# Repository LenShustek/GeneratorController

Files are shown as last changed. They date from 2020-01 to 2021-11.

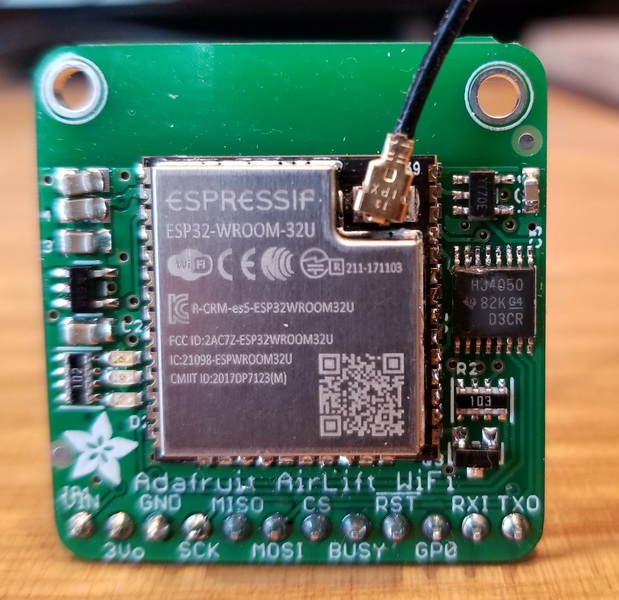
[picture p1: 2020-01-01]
photos/remade_Airlift.jpg

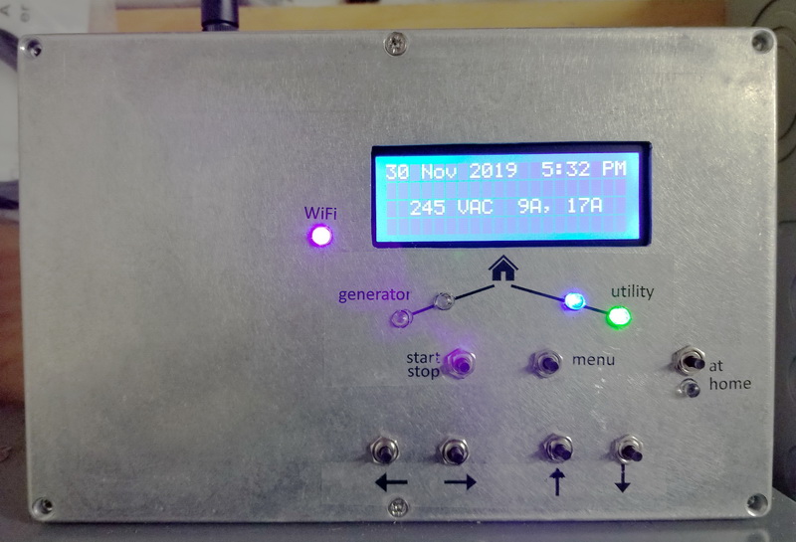
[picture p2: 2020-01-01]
photos/box_outside.jpg

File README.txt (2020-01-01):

This is the hardware and software design for an external custom 
controller for Cummins standby power generators and transfer switches. 

We have a couple of these generators in locations which are unoccupied 
for long periods of time. The normal operation of the standard 
setup is to run the generator whenever the power is out, until 
either the power returns or the fuel runs out. 

What we want instead, when the property is not occupied, is for the 
generator to run enough to keep the food in the freezers cold, but not 
to run all the time. That conserves fuel, and annoys the neighbors less. 

Our custom controller works like this: after the power fails, it waits 
for a few hours to see if the power comes back. If it doesn't, it runs 
the generator for 30 minutes every few hours so that the freezers are 
kept cold. If someone is home and wants the power to be on all the time, 
there is an "at home" button on the front panel that does that. All the 
times are, of course, configurable. 

The controller also has a WiFi interface and acts as a web server, so 
you can use a browser from a remote location to check the status and 
make changes. (That depends, of course, on whether your location has 
internet access without utility power or when on generator power.) It 
can also send a text message and/or an email when power fails or is 
restored, using the IFTTT ("If This Then That") free service. 

Other features:
  - display of the utility and generator voltage levels (0-250 VAC)
  - display of the load current on each of two phases (0-100A)
  - display of the starter battery voltage after the power fails,
    when it is not being charged
  - a configurable generator exercise schedule
  - a realtime clock with battery backup
  - non-volatile memory for configuration information and an event log
  - a hardware watchdog timer that restarts the processor if something 
    locks up the controller
  - manual operation of the generator and transfer switch for testing
  
We have this installed and running with these two generator/switch configurations:
  - Cummins RS22 22 kW generator with the RA100A automatic transfer switch
    (smart generator, dumb switch)
  - Cummins RS30000 30 kW generator with the RSS100 automatic transfer switch "with controller"
    (dumb generator, smart switch)
  
See more information in the "design notes" file and in the source code comments.

This is a non-trivial amateur construction project, and the design here comes, of course,
with no guarantee that it will work for you. That said, we are happy with the way it 
works for us.

Len Shustek
December 2019

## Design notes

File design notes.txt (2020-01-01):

DESIGN NOTES FOR A CUSTOM CUMMINS GENERATOR CONTROLLER

Which generators and transfer switches I'm using
------------------------------------------------

I built two of these controllers for two locations with different equipment from 
Cummins. In all cases, note that the ATS ("automatic transfer switch") design 
only allows it to switch to a supply (utility or generator) that has power. 

(1) RS22 22 kW generator and the RA100A transfer switch 

In this case the generator is smart; it controls an engine cooldown period and 
maintains its own exercise schedule. It responds to a "start generator" command 
and provides a "generator ready" status. 

The switch is dumb and only reacts to an "activate switch" input. It supplies 
contact closures to indicate which way the switch is positioned, and whether the 
utility power is present. We install only voltage and current sensors in the 
switch, plus a bunch of wires. 

(2) RS30000 30 kW generator and the RSS100 transfer switch "with controller" 

In this case the generator is primitive; it obeys a "start generator" command 
and does nothing else. No exercise periods, no engine cooldown, no "generator 
ready" status. 

The switch, on the other hand, is smart, with a microprocessor and some lights 
and buttons. Their processor chooses the switch position, starts the generator, 
enforces a cooldown period, and can establish an exercise schedule. We take over 
the "generator start" line, but otherwise let the switch processor do its 
thing. Our "connect to generator" relay output is not used. In addition to 
voltage and current sensors, we install relays that provide contact closures so 
we know whether utility and/or generator power is present. 

When power fails, the ATS waits for generator power to be present before 
activating the switch. Since we might delay starting the generator, it will 
follow that delay. When we "rest" the generator, it leaves the switch alone as 
long as utility power isn't present. The result is that our normal 
"wait-run-rest-run" cycle works fine. 

When utility power returns, it waits for TDEN ("time delay emergency to 
normal"), which defaults to 10 minutes, before switching back to utility power. 
Our "utility return delay" should therefore be at least that long so we don't 
turn off the generator prematurely. See the Cummins "RSS100 and RSS200 Transfer
Switch Service Manual" for instructions on setting TDEN to 5 minutes instead.

We have taken over the "generator start" control line, so we need to implement 
both an exercise schedule and an engine cooldown time, because their controller 
can no longer do those. 

In a future version of the controller we could add a third relay so that we can 
separately control "connect to utility" and "connect to generator"; then we are 
not dependent on the TDEN 10 minute delay to connect to the utility. That would
require that we connect those control lines to us instead of their processor.
It may not be worth it.

Changes we make inside the ATS (automatic transfer switch) include:
-------------------------------------------------------------------

 - connect our control/status and sense wire harnesses to various points
   inside the switch
 - add a toggle switch that powers down our controller and returns to 
   the normal factory mode of operation
 - add two ferrite transducers around the house power cables that 
   measure current draw of the load
 - add two transducers that measure the generator and utility voltage
 - for the RSS version, add two 240 VAC relays to indicate whether 
   utility and/or generator power is present
 
Design of the controller board
------------------------------

On one side of the PC board there are 7 pushbutton switches, a 20x4 LCD display, 
and 6 LED indicators. It mounts directly to the front panel of the metal 
enclosure using the switch nuts. The panel has holes for the switches and LEDs, 
and a rectangular cutout for the LCD display. 

The other side of the board contains all the other components including the two 
harness connectors to the transfer switch, and the Wifi antenna connection on 
the Airlift Wifi board. Many of the components are surface-mount, but I chose 
largish versions (1/4 watt resistors instead of 1/8 watt, for example) so that 
it's relatively easy to hand solder. 

The Airlift board is a special version of the Adafruit product I built which 
uses the ESP32 version that has a U.FL connector for an external antenna. 

Electrical noise mitigation
---------------------------

Being located adjacent to a box where 100+ amps of power is switched in 
milliseconds causes all sorts of wired and wireless RFI electrical noise 
that can disrupt the electronics of our controller. Here are the steps 
I took to mitigate that problem: 

- a metal enclosure for the circuit board
- an MOV transient voltage suppressor on the power input
- a large low-pass inductor and big filtering caps on the power input
- a diode array transient voltage suppressor on signals from outside the box
- optical isolation for digital input signals
- ground plane pours on both side of the PC board
- transparent conductive film over the cutout for the LCD display
- a deadman watchdog timer that resets the processor if it becomes catatonic
- code that resets the LCD display whenever the power is switched

That seems to have fixed the problem, but I have no idea which items were 
most important and how much margin there is.

Len Shustek
December 2019

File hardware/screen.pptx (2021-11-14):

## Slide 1

7.9”

power went off at
12 Mar 9:23 AM
generator goes on in
1 hr 12 min 15 sec

generator

generator
start/stop

menu

utility

4.7”

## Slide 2

for web page

generator

generator
start/stop

menu

utility

at
home

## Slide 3

for aluminum box

WiFi

generator

start
stop

utility

menu

at
home

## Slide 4

WiFi

generator

start
stop

utility

menu

generator

start
stop

utility

menu

WiFi

at
home

at
home

Generator control

Generator control

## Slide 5

Saw Mill Lodge
230 VAC, 54/33 A

power went off at
12 Mar 2019 9:23 AM
generator goes on in
1 hr 12 min 15 sec

12 Mar 2019 9:23 AM
230 VAC, 54/33 A

power went off at
12 Mar 9:23 AM generator starting

start generator?
press
“Generator start”
to confirm

power went off at
12 Mar 9:23 AM
connecting generator

set parameter:
gen start delay
120 mins

set time and date
12 Mar 9:32 AM

event log
#12: 12 Mar 9:23 AM
power failed

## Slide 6

generator running
238 VAC, 54/33 A
will go off in
23 min 12 sec

generator running
238 VAC, 54/33 A
2 hr 39 min 44 sec

generator running
238 VAC, 54/33 A
2 hr 39 min 44 sec
util in 2 min 15 sec

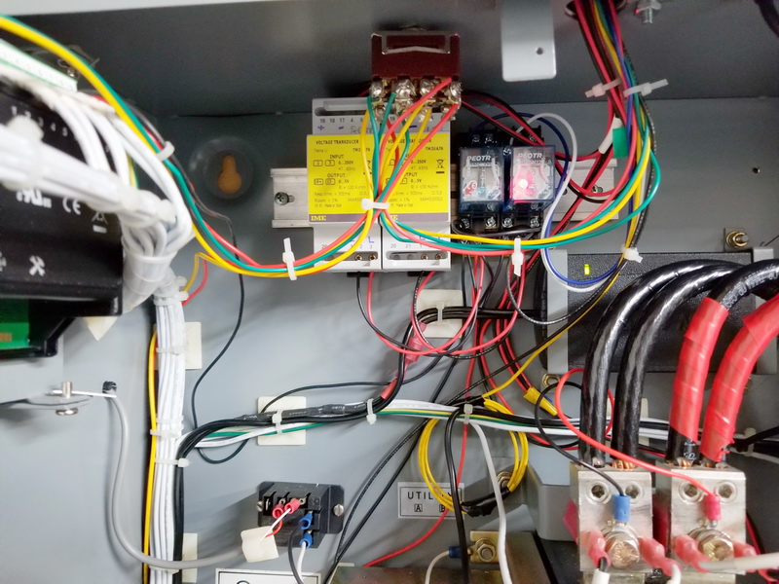
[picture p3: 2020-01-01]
photos/RSS_transfer_switch_mods.jpg

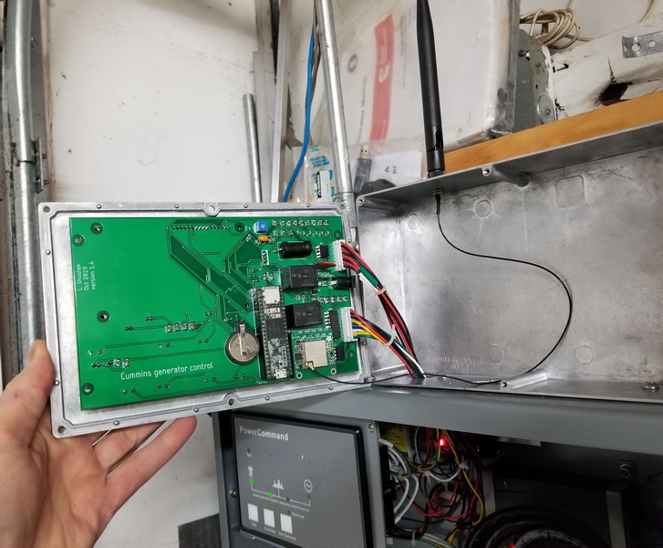
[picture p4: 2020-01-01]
photos/box_inside.jpg

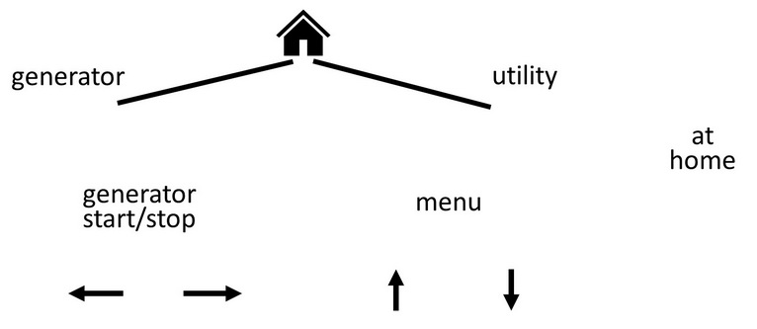
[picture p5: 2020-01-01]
src/controller/buttonimage.jpg

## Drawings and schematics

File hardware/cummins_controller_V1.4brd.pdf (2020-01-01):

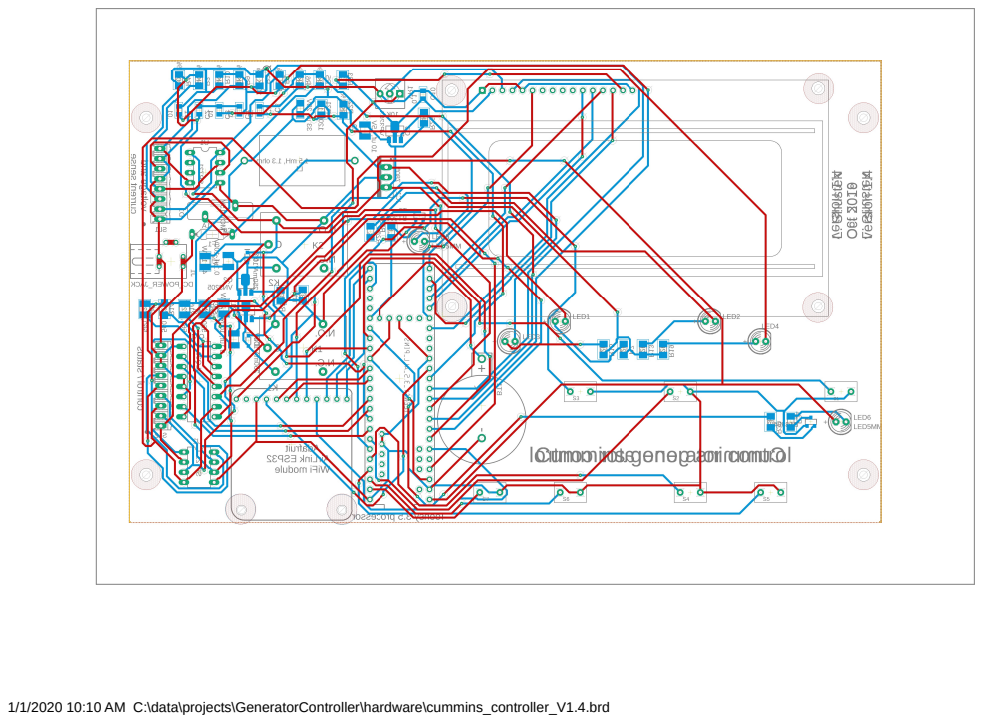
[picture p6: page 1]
current sense

1/1/2020 10:10 AM C:\data\projects\GeneratorController\hardware\cummins_controller_V1.4.brd

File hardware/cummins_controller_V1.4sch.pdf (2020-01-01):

10 uf, 15V | VCC GND | 10K

# 1A VCC

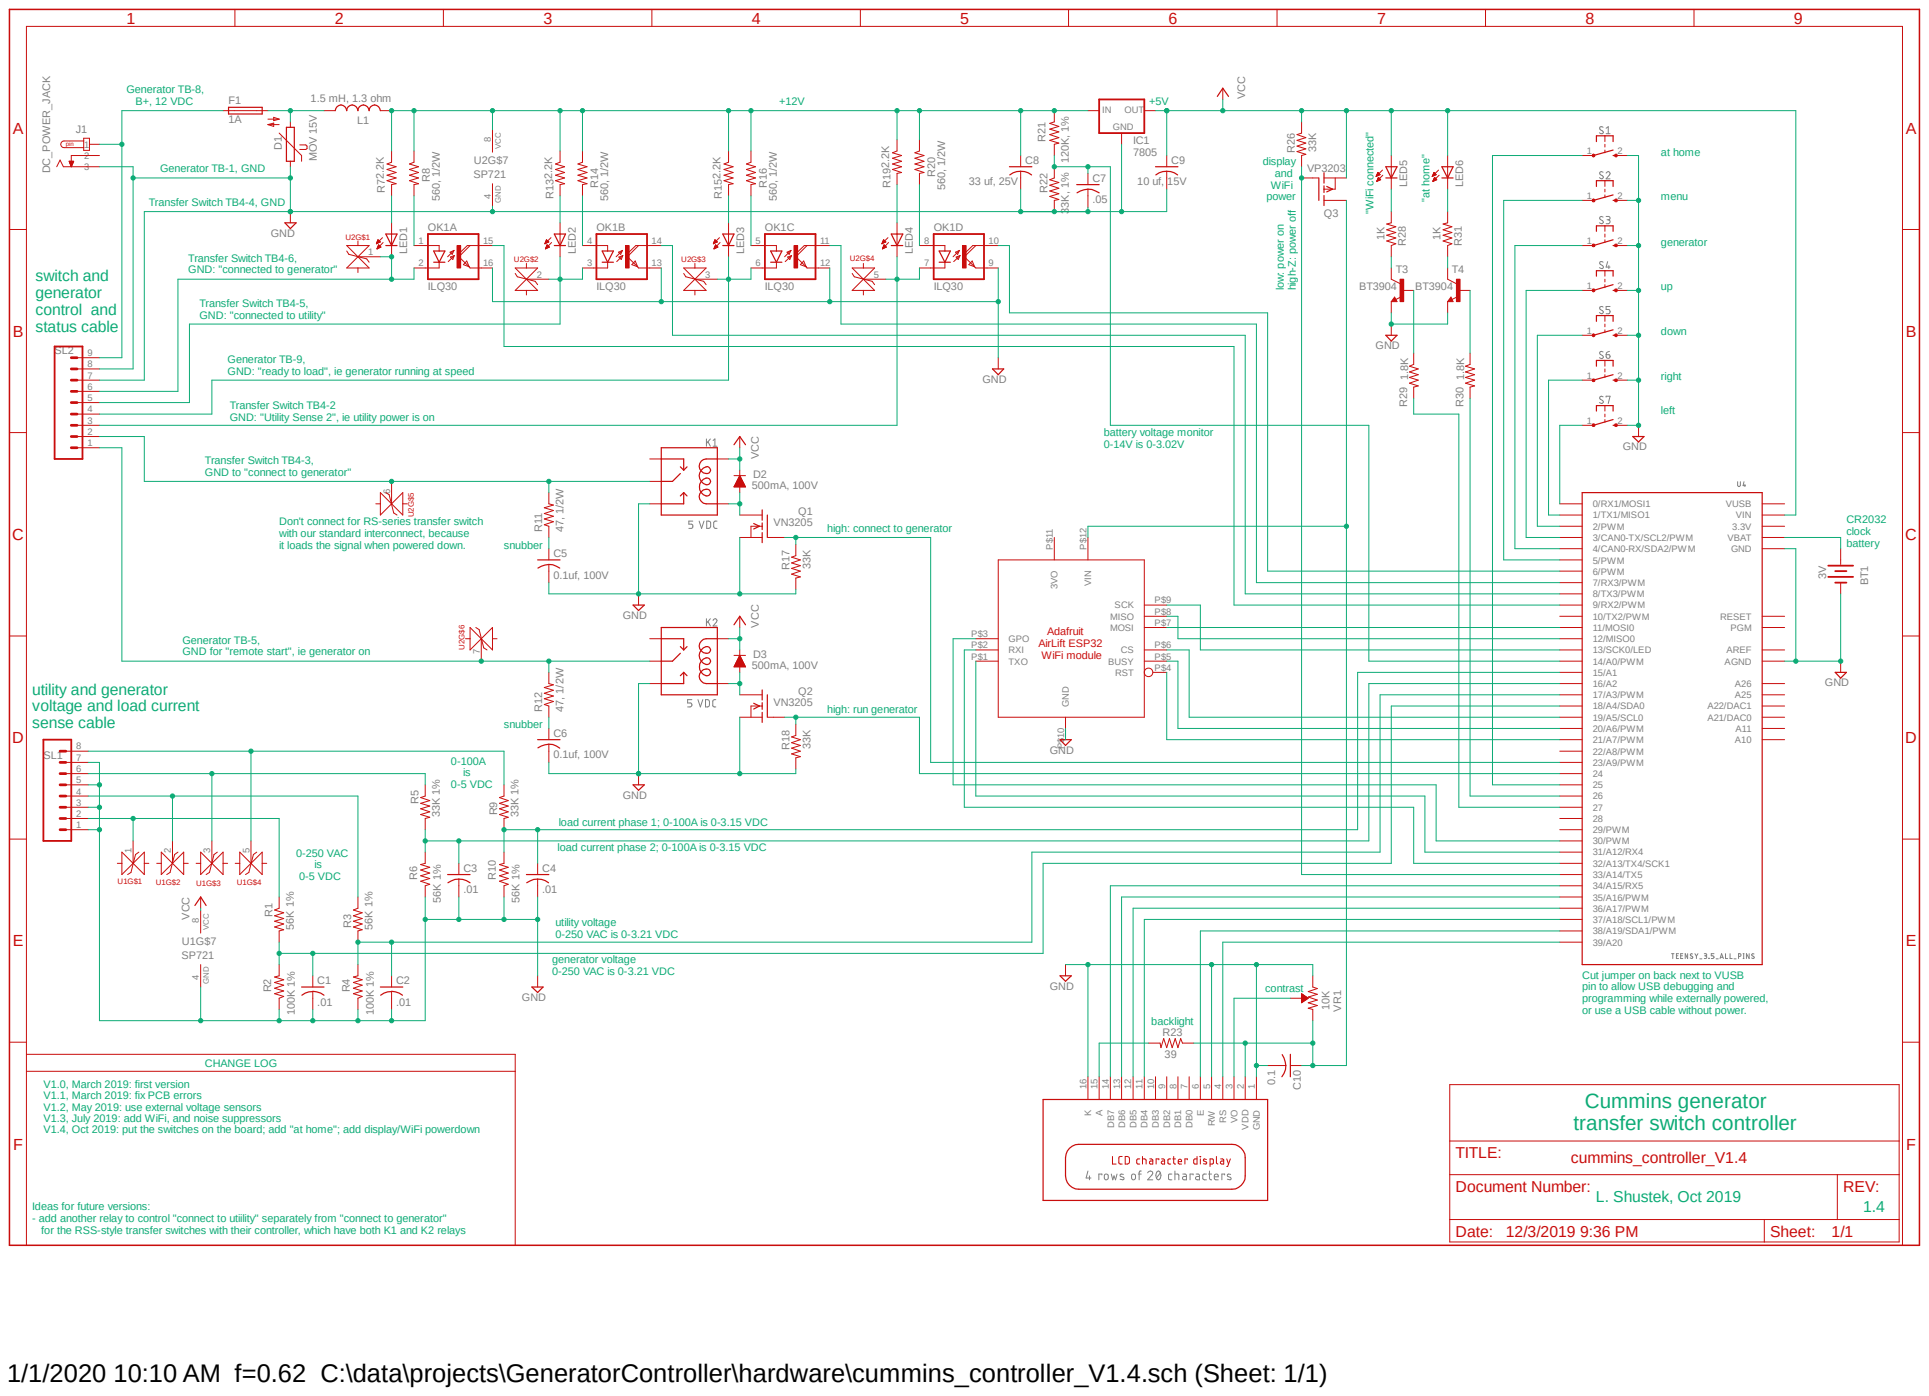
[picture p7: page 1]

Transfer Switch TB4-5, GND: "connected to utility" Generator TB-8,
B+, 12 VDC

pin to allow USB debugging and programming while externally powered, or use a USB cable without power. "WiFi connected"

at home Don't connect for RS-series transfer switch with our standard interconnect, because

Transfer Switch TB4-4, GND Generator TB-1, GND

Transfer Switch TB4-6, GND: "connected to generator" Generator TB-5, GND for "remote start", ie generator on Transfer Switch TB4-3, GND to "connect to generator" Generator TB-9, GND: "ready to load", ie generator running at speed

Transfer Switch TB4-2 GND: "Utility Sense 2", ie utility power is on

battery voltage monitor 0-14V is 0-3.02V

high: run generator high: connect to generator

it loads the signal when powered down.

utility and generator
voltage and load current
sense cable

load current phase 1; 0-100A is 0-3.15 VDC

load current phase 2; 0-100A is 0-3.15 VDC

Date: Sheet: L. Shustek, Oct 2019 | REV: TITLE: Document Number: 1.4

Ideas for future versions: - add another relay to control "connect to utiility" separately from "connect to generator"
for the RSS-style transfer switches with their controller, which have both K1 and K2 relays

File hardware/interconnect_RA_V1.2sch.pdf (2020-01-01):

A

A

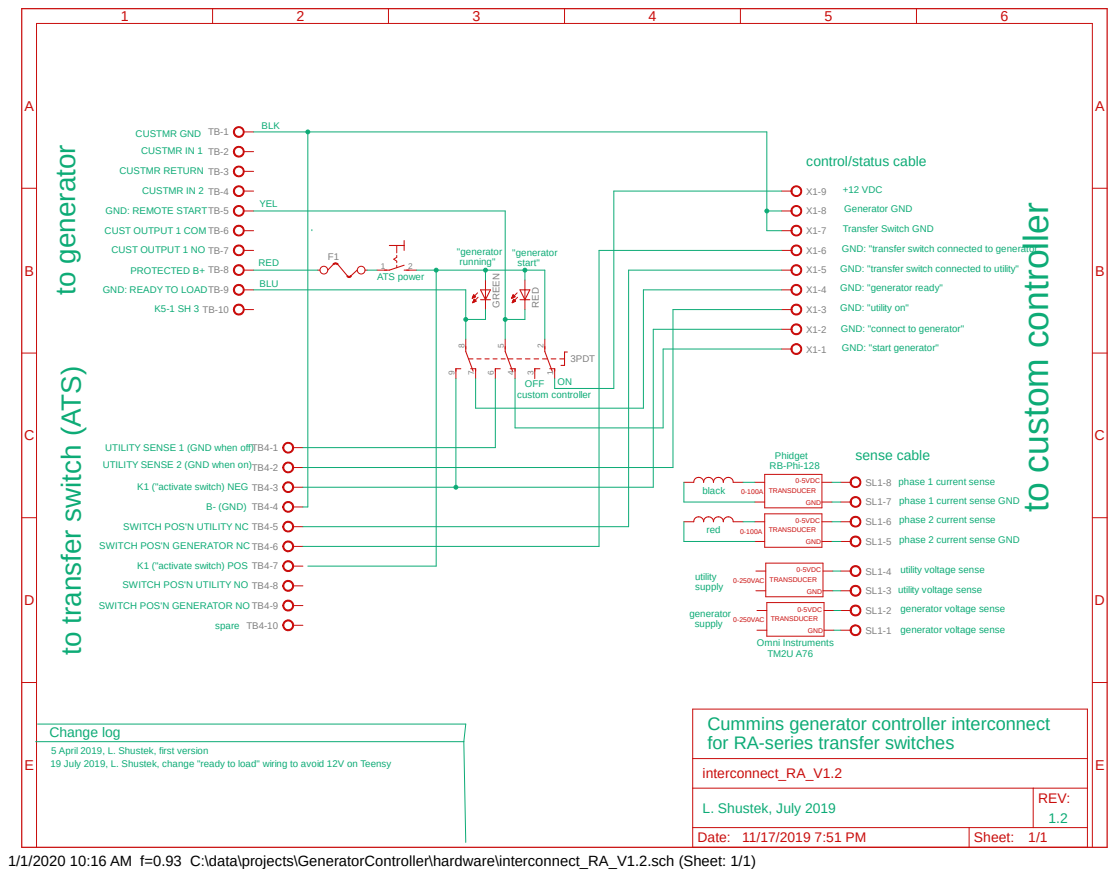
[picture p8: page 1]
3PDT; GREEN; RED; interconnect_RA_V1.2; 0-5VDC GND; TRANSDUCER; 0-250VAC; sense cable; to custom controller to generator to transfer switch ⁽ATS⁾; CUSTMR GND; CUSTMR IN 1; CUSTMR RETURN; CUSTMR IN 2; B- (GND); spare; generator supply; utility supply; custom controller; OFF; Omni Instruments TM2U A76; Phidget RB-Phi-128; red; black; BLK; YEL; BLU; ATS power; "generator start"; "generator running"

control/status cable

+12 VDC
Generator GND
Transfer Switch GND
GND: "transfer switch connected to generator"
GND: "transfer switch connected to utility"
GND: "generator ready"
GND: "utility on"
GND: "connect to generator"
GND: "start generator"

GND: REMOTE START
CUST OUTPUT 1 COM
CUST OUTPUT 1 NO
PROTECTED B+
GND: READY TO LOAD

UTILITY SENSE 1 (GND when off)
UTILITY SENSE 2 (GND when on)

phase 1 current sense
phase 1 current sense GND
phase 2 current sense
phase 2 current sense GND

K1 ("activate switch) NEG

SWITCH POS'N UTILITY NC
SWITCH POS'N GENERATOR NC

K1 ("activate switch) POS
SWITCH POS'N UTILITY NO
SWITCH POS'N GENERATOR NO

utility voltage sense

generator voltage sense

Cummins generator controller interconnect
for RA-series transfer switches

Change log
5 April 2019, L. Shustek, first version
19 July 2019, L. Shustek, change "ready to load" wiring to avoid 12V on Teensy

L. Shustek, July 2019 | REV: 1.2

Date: 11/17/2019 7:51 PM | Sheet: 1/1

1/1/2020 10:16 AM f=0.93 C:\data\projects\GeneratorController\hardware\interconnect_RA_V1.2.sch (Sheet: 1/1)

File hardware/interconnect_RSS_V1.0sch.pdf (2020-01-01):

A

A

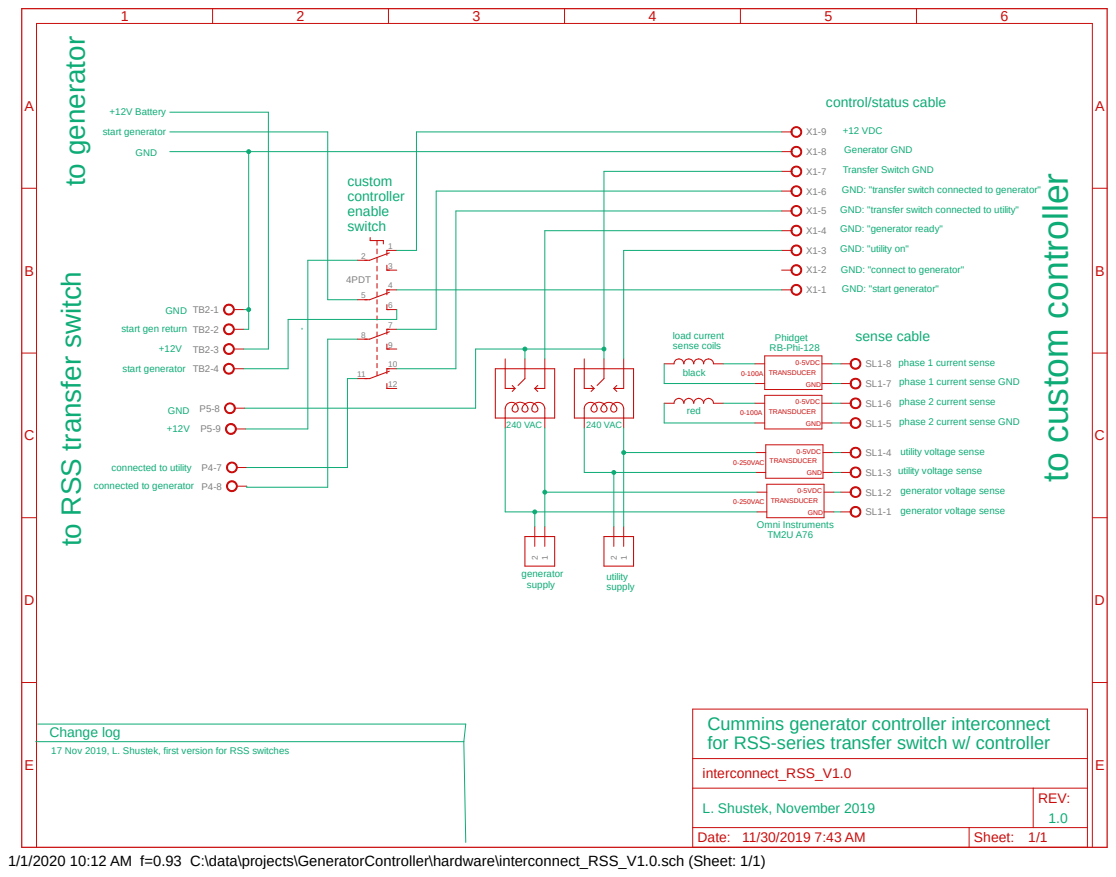
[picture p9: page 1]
4PDT; interconnect_RSS_V1.0; 0-5VDC GND; TRANSDUCER; 0-250VAC; sense cable; to custom controllerto generator to RSS transfer switch; GND; start generator; utility voltage sense; generator; supply; utility; Omni Instruments TM2U A76; Phidget RB-Phi-128; red; black; custom controller enable switch; 240 VAC; load current sense coils; +12V Battery

control/status cable

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

start gen return

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

connected to utility
connected to generator

generator voltage sense

Cummins generator controller interconnect
for RSS-series transfer switch w/ controller

Change log
17 Nov 2019, L. Shustek, first version for RSS switches

L. Shustek, November 2019 | REV: 1.0

Date: 11/30/2019 7:43 AM | Sheet: 1/1

1/1/2020 10:12 AM f=0.93 C:\data\projects\GeneratorController\hardware\interconnect_RSS_V1.0.sch (Sheet: 1/1)

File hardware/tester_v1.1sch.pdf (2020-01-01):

A

A

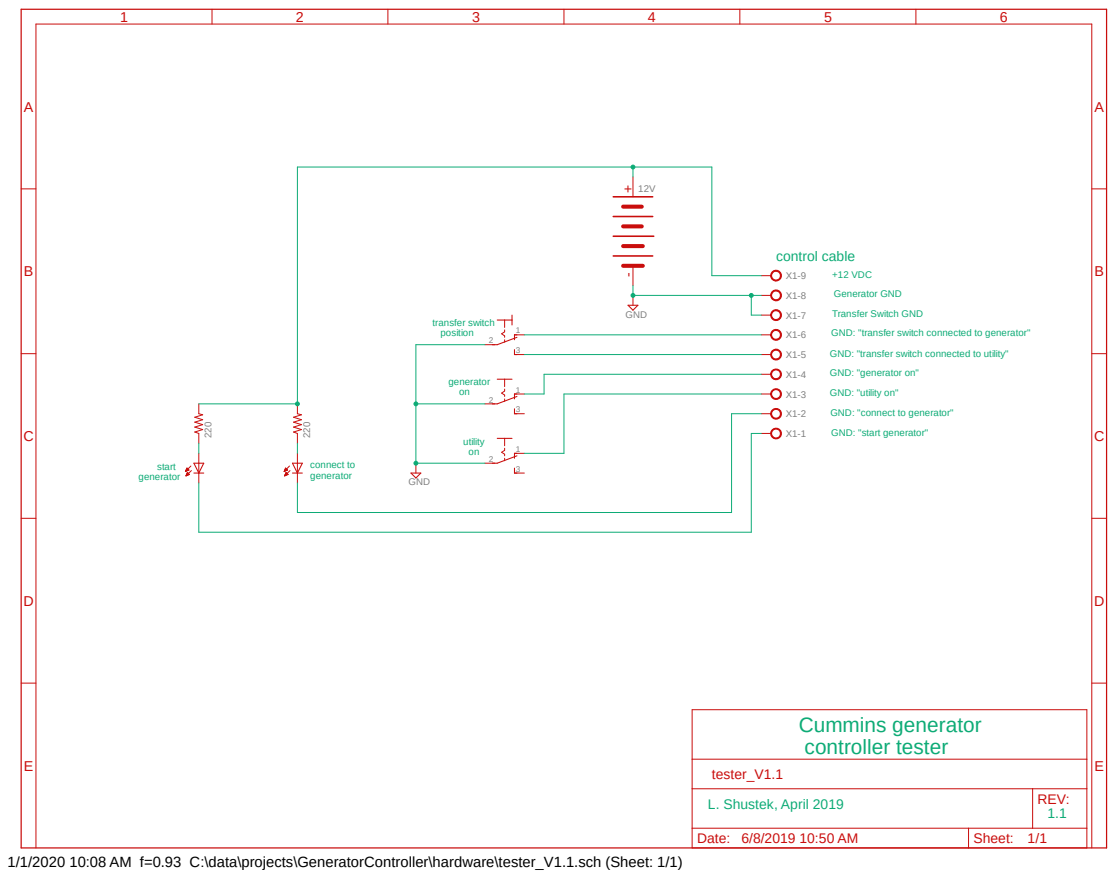
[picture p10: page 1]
GND; tester_V1.1 ⁻ ⁺; Cummins generator controller tester; control cable; transfer switch position; generator on; start generator; connect to; generator; utility on

+12 VDC
Generator GND
Transfer Switch GND
GND: "transfer switch connected to generator"
GND: "transfer switch connected to utility"
GND: "generator on"
GND: "utility on"
GND: "connect to generator"
GND: "start generator"

L. Shustek, April 2019 | REV: 1.1

Date: 6/8/2019 10:50 AM | Sheet: 1/1

1/1/2020 10:08 AM f=0.93 C:\data\projects\GeneratorController\hardware\tester_V1.1.sch (Sheet: 1/1)

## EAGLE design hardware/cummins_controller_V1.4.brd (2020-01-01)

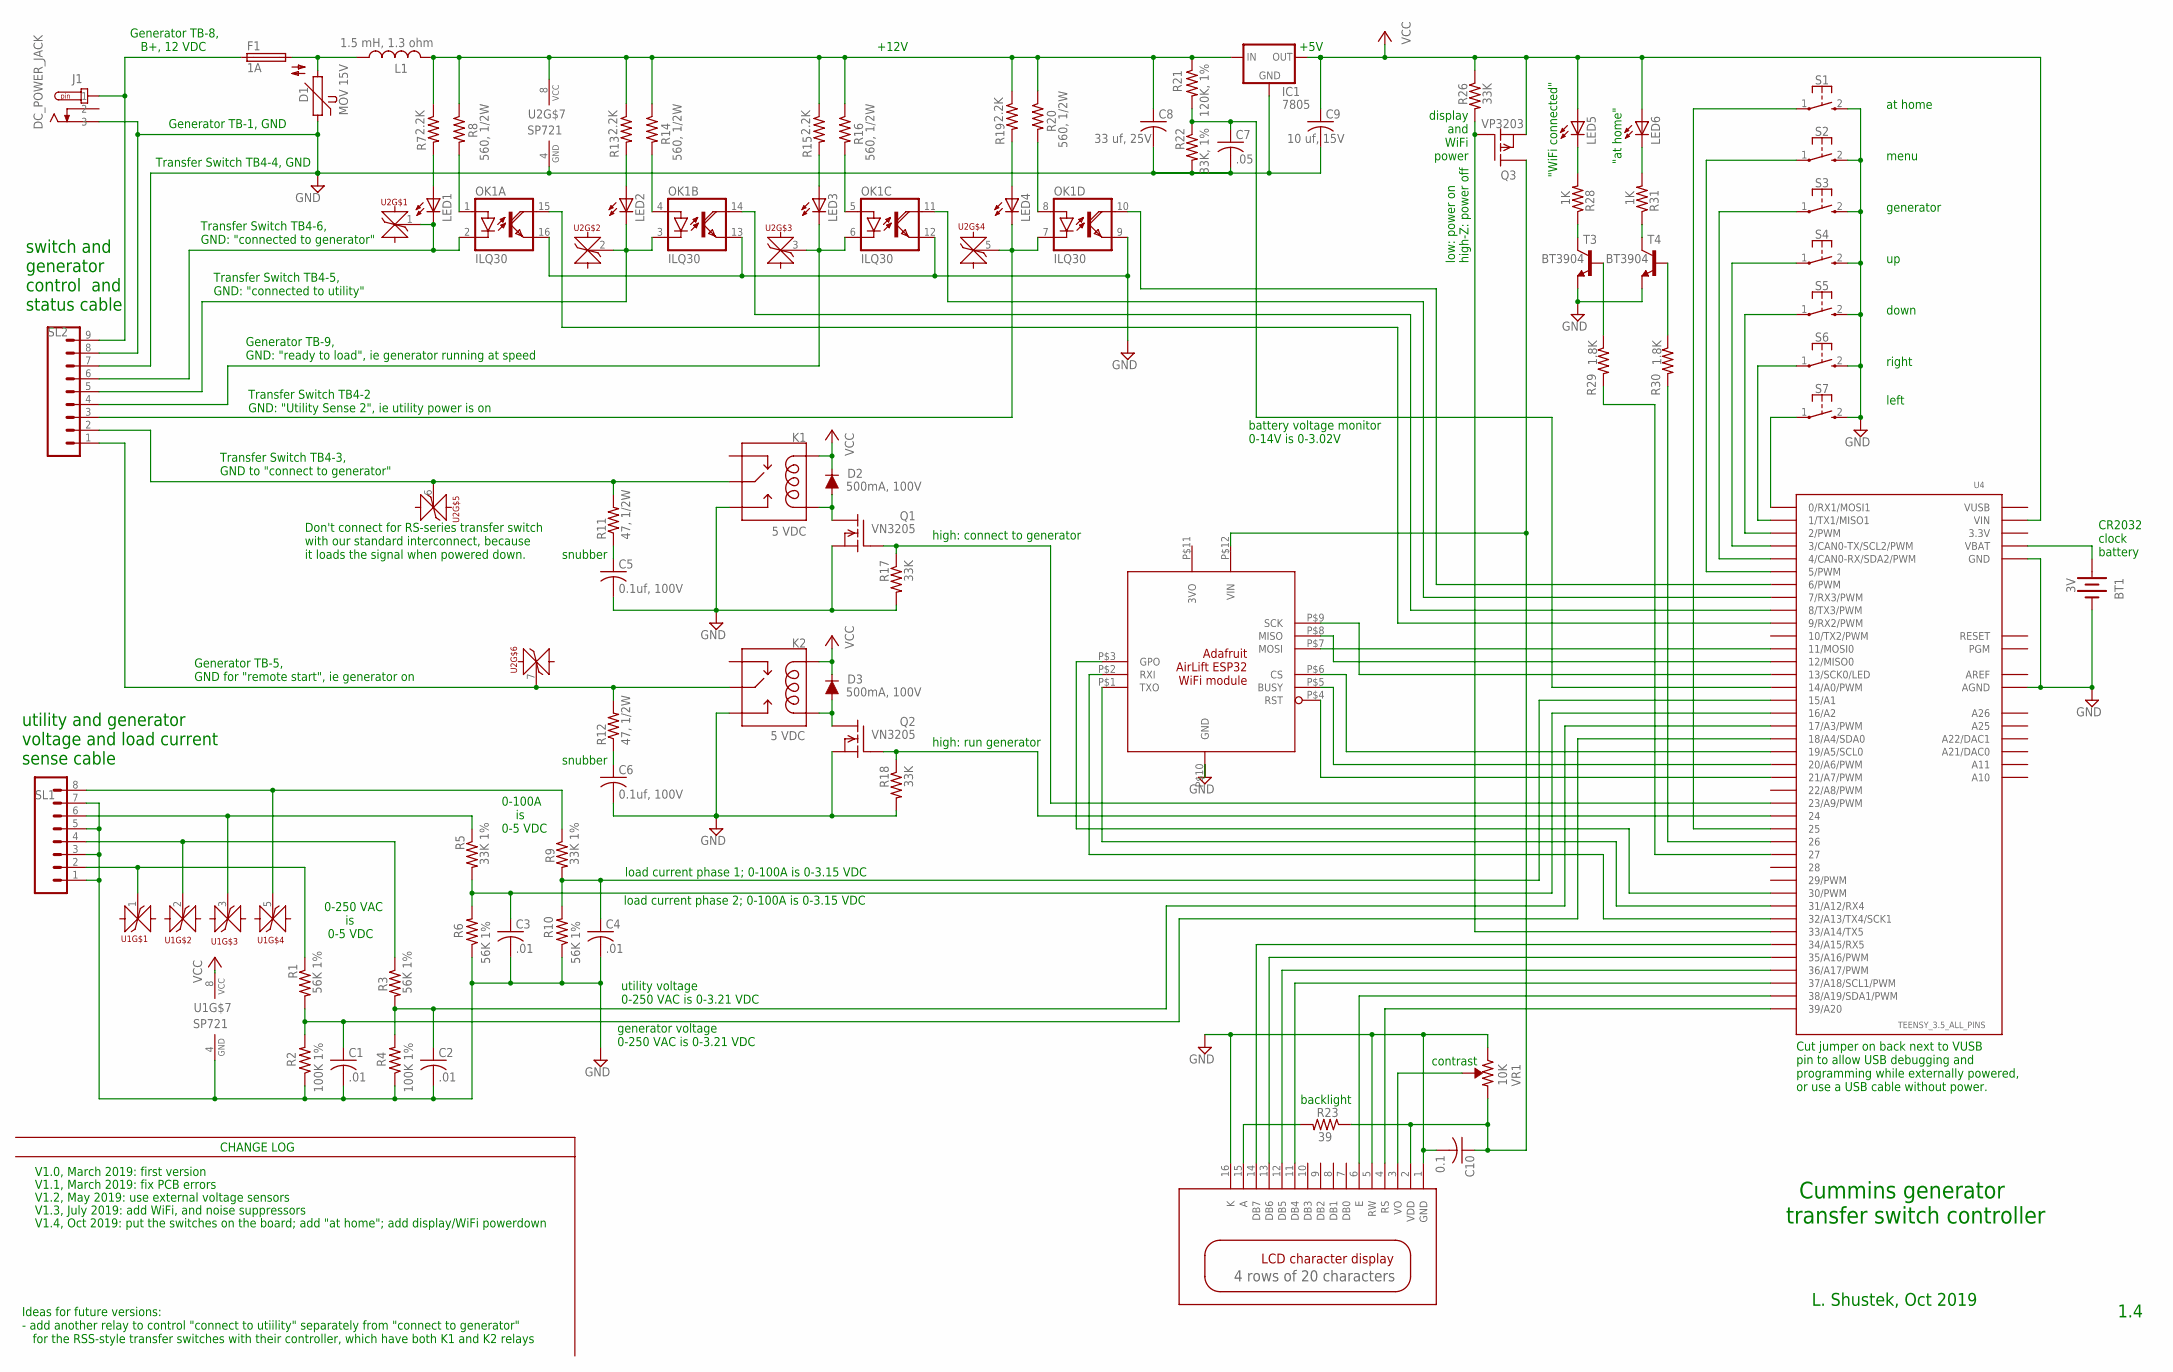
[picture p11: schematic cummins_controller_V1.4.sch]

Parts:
BT1: 3V; BATTCOM_20MM_PTH
C1, C2, C3, C4: .01; C0805K
C5, C6: 0.1uf, 100V; C1210K
C7: .05; C0805K
C8: 33 uf, 25V; C3216
C9: 10 uf, 15V; C1210K
C10: 0.1; C0805K
D1: MOV 15V; S14K230
D2, D3: 500mA, 100V; SOD-323
F1: 1A; PICOFUSE
IC1: 7805; 78XXS
J1: DC_POWER_JACK
K1, K2: 5 VDC; RELAY-PANASONIC-JS
L1: 1.5 mH, 1.3 ohm; INDUCTOR_1.1IN
LED1, LED2, LED3, LED4, LED5, LED6: LED5MM
OK1: ILQ30; DIL16
Q1, Q2: VN3205; SOT89
Q3: VP3203; SOT89
R1, R3, R6, R10: 56K 1%; M1206
R2, R4: 100K 1%; M1206
R5, R9: 33K 1%; M1206
R7, R13, R15, R19: 2.2K; M1206
R8, R16, R20: 560, 1/2W; R1210
R11, R12: 47, 1/2W; R1210
R14: 560, 1/2W; R1210W
R17, R18, R26: 33K; M1206
R21: 120K, 1%; M1206
R22: 33K, 1%; M1206
R23: 39; M1206
R28, R31: 1K; M1206
R29, R30: 1.8K; M1206
S1, S2, S3, S4, S5, S6, S7: PUSHBUTTON-SPST
SL1: M08; 08P
SL2: M09; 09P
T3, T4: BT3904; SOT23-3
U1, U2: SP721; TVS_6DIODE_ARRAY
U3: ADAFRUIT_AIRLIFT_ESP32
U4: TEENSY_3.5_ALL_PINS
VR1: 10K; TRIMBOT-BOURNS-3362M
X1: 4 rows of 20 characters; LCD-CHARACTER-DISPLAY-20X4

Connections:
3.3V: U4.3.3V, U4.3.3V3 (3.3V), U4.3.3V4 (3.3V)
AREF: U4.AREF
GND: BT1.2 (-), C1.2, C2.2, C3.2, C4.2, C5.2, C6.2, C7.2, C8.2, C9.2, C10.2, D1.1, IC1.GND, J1.P$5 (3), K1.P$3 (NO), K2.P$3 (NO), OK1.9 (EMI), OK1.12 (EMI), OK1.13 (EMI), OK1.16 (EMI), Q1.3 (S), Q2.3 (S), R2.1, R4.1, R6.1, R10.1, R17.2, R18.2, R22.2, S1.2 (3), S2.2 (3), S3.2 (3), S4.2 (3), S5.2 (3), S6.2 (3), S7.2 (3), SL1.1, SL1.3, SL1.5, SL1.7, SL2.7, SL2.8, T3.2 (E), T4.2 (E), U1.4 (GND), U2.4 (GND), U3.P$10 (GND), U4.AGND, U4.GND, U4.GND1 (GND), U4.GND3 (GND), U4.GND4 (GND), U4.GND6 (GND), VR1.3 (CW), X1.1 (GND), X1.5 (RW), X1.16 (K)
unnamed: BT1.1 (+), U4.VBAT
unnamed: D2.A, K1.P$5 (COIL2), Q1.2 (D), Q1.2@1 (D)
unnamed: S7.1, U4.0 (0/RX1/MOSI1)
unnamed: LED1.A, R7.2
unnamed: R9.1, SL1.8, U1.5
unnamed: D3.A, K2.P$5 (COIL2), Q2.2 (D), Q2.2@1 (D)
unnamed: U3.P$1 (TXO), U4.31/A12 (31/A12/RX4)
unnamed: LED2.K (C), OK1.3 (C), SL2.5, U2.2
unnamed: F1.1, J1.P$1 (1), SL2.9
unnamed: LED2.A, R13.2
unnamed: K2.P$1 (MAIN), R12.2, SL2.1, U2.7
unnamed: K1.P$1 (MAIN), R11.2, SL2.2, U2.6
unnamed: LED3.A, R15.2
unnamed: Q2.1 (G), R18.1, U4.24
unnamed: C4.1, R9.2, R10.2, U4.15/A1
unnamed: R5.1, SL1.6, U1.3
unnamed: C3.1, R5.2, R6.2, U4.16/A2
unnamed: R3.1, SL1.4, U1.2
unnamed: C2.1, R3.2, R4.2, U4.17/A3 (17/A3/PWM)
unnamed: LED4.A, R19.2
unnamed: OK1.5 (A), R16.2
unnamed: R1.1, SL1.2, U1.1
unnamed: R30.1, T4.1 (B)
unnamed: LED1.K (C), OK1.2 (C), SL2.6, U2.1
unnamed: C1.1, R1.2, R2.2, U4.18/A4 (18/A4/SDA0)
unnamed: U3.P$9 (SCK), U4.13 (13/SCK0/LED)
unnamed: U3.P$8 (MISO), U4.12 (12/MISO0)
unnamed: U3.P$7 (MOSI), U4.11 (11/MOSI0)
unnamed: U3.P$6 (CS), U4.19/A5 (19/A5/SCL0)
unnamed: U3.P$5 (BUSY), U4.20/A6 (20/A6/PWM)
unnamed: U3.P$4 (RST), U4.21/A7 (21/A7/PWM)
unnamed: U3.P$2 (RXI), U4.32/A13 (32/A13/TX4/SCK1)
unnamed: U4.34/A15 (34/A15/RX5), X1.14 (DB7)
unnamed: R31.1, T4.3 (C)
unnamed: U4.39/A20, X1.4 (RS)
unnamed: U4.38/A19 (38/A19/SDA1/PWM), X1.6 (E)
unnamed: LED3.K (C), OK1.6 (C), SL2.4, U2.3
unnamed: U4.37/A18 (37/A18/SCL1/PWM), X1.11 (DB4)
unnamed: U4.36/A17 (36/A17/PWM), X1.12 (DB5)
unnamed: U4.35/A16 (35/A16/PWM), X1.13 (DB6)
unnamed: Q1.1 (G), R17.1, U4.23/A9 (23/A9/PWM)
unnamed: C8.1, IC1.IN, L1.P$2 (2), R7.1, R8.1, R13.1, R14.1, R15.1, R16.1, R19.1, R20.1, R21.1, U2.8 (VCC)
unnamed: S6.1, U4.1 (1/TX1/MISO1)
unnamed: S5.1, U4.2 (2/PWM)
unnamed: S4.1, U4.3 (3/CAN0-TX/SCL2/PWM)
unnamed: S3.1, U4.4 (4/CAN0-RX/SDA2/PWM)
unnamed: S2.1, U4.5 (5/PWM)
unnamed: VR1.2 (WIPER), X1.3 (VO)
unnamed: R23.2, X1.15 (A)
unnamed: S1.1, U4.25
unnamed: LED5.K (C), R28.2
unnamed: OK1.10 (COL), U4.6 (6/PWM)
unnamed: OK1.11 (COL), U4.7 (7/RX3/PWM)
unnamed: OK1.14 (COL), U4.8 (8/TX3/PWM)
unnamed: OK1.15 (COL), U4.9 (9/RX2/PWM)
unnamed: C5.1, R11.1
unnamed: C6.1, R12.1
unnamed: OK1.1 (A), R8.2
unnamed: LED4.K (C), OK1.7 (C), SL2.3, U2.5
unnamed: OK1.4 (A), R14.2
unnamed: LED6.K (C), R31.2
unnamed: OK1.8 (A), R20.2
unnamed: C7.1, R21.2, R22.1, U4.14/A0 (14/A0/PWM)
unnamed: Q3.1 (G), R26.2, U4.33/A14 (33/A14/TX5)
unnamed: U3.P$3 (GPO), U4.30 (30/PWM)
unnamed: R29.1, T3.1 (B)
unnamed: R28.1, T3.3 (C)
unnamed: R29.2, U4.27
unnamed: D1.2, F1.2, L1.P$1 (1)
unnamed: R30.2, U4.26
VCC: C9.1, D2.C, D3.C, IC1.OUT, K1.P$2 (COIL1), K2.P$2 (COIL1), LED5.A, LED6.A, Q3.3 (S), R26.1, U1.8 (VCC), U4.VIN
VDD: C10.1, Q3.2 (D), Q3.2@1 (D), R23.1, U3.P$12 (VIN), VR1.1 (CCW), X1.2 (VDD)
VUSB: U4.VUSB

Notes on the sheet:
utility voltage 0-250 VAC is 0-3.21 VDC
generator voltage 0-250 VAC is 0-3.21 VDC
Cummins generator transfer switch controller
L. Shustek, Oct 2019
backlight
+5V
1.4
CR2032 clock battery
contrast
Transfer Switch TB4-5, GND: "connected to utility"
Generator TB-8, B+, 12 VDC
Transfer Switch TB4-4, GND
Generator TB-1, GND
Transfer Switch TB4-6, GND: "connected to generator"
Generator TB-5, GND for "remote start", ie generator on
Transfer Switch TB4-3, GND to "connect to generator"
Generator TB-9, GND: "ready to load", ie generator running at speed
high: run generator
high: connect to generator
switch and generator control and status cable
utility and generator voltage and load current sense cable
load current phase 1; 0-100A is 0-3.15 VDC
load current phase 2; 0-100A is 0-3.15 VDC
0-100A is 0-5 VDC
battery voltage monitor 0-14V is 0-3.02V
snubber
Transfer Switch TB4-2 GND: "Utility Sense 2", ie utility power is on
0-250 VAC is 0-5 VDC
CHANGE LOG
V1.0, March 2019: first version
V1.1, March 2019: fix PCB errors
V1.2, May 2019: use external voltage sensors
V1.3, July 2019: add WiFi, and noise suppressors
Cut jumper on back next to VUSB pin to allow USB debugging and programming while externally powered, or use a USB cable without power.
"WiFi connected"
V1.4, Oct 2019: put the switches on the board; add "at home"; add display/WiFi powerdown
low: power on high-Z: power off
display and WiFi power
+12V
"at home"

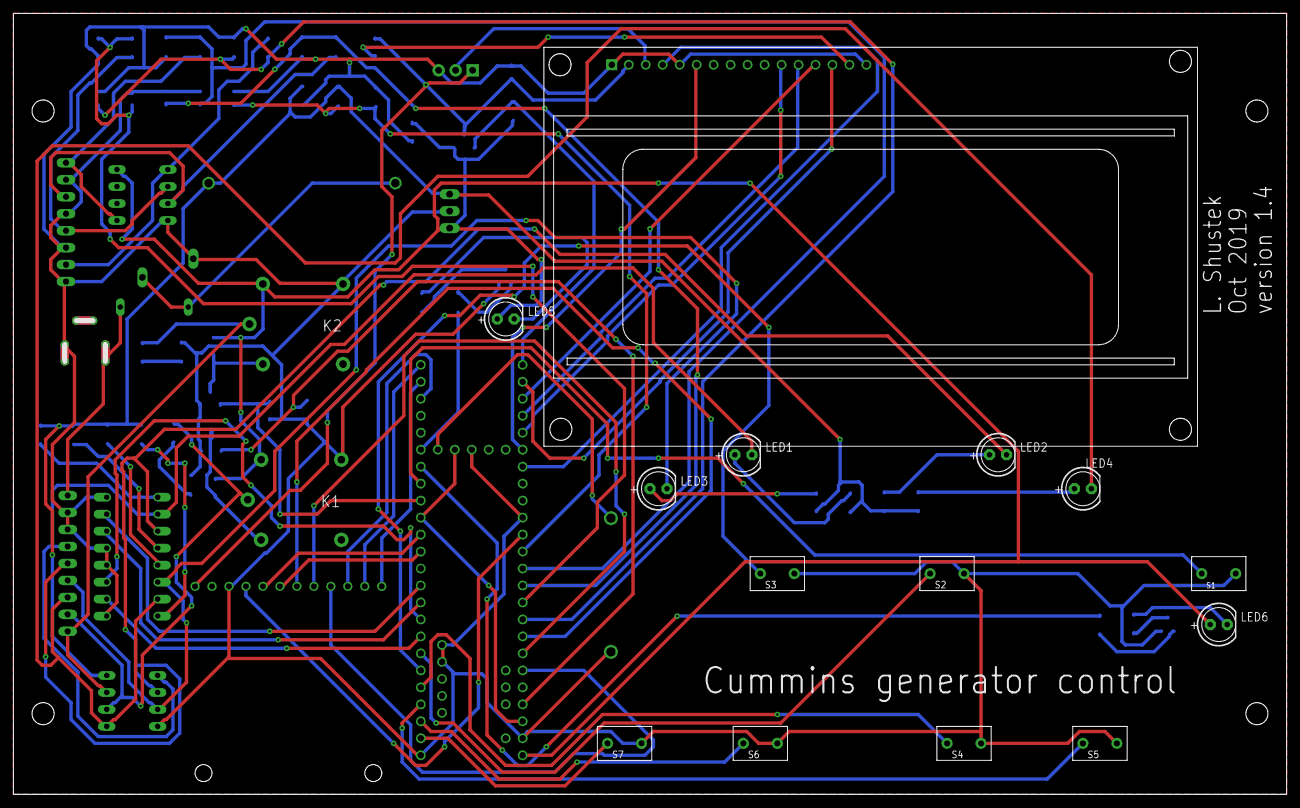
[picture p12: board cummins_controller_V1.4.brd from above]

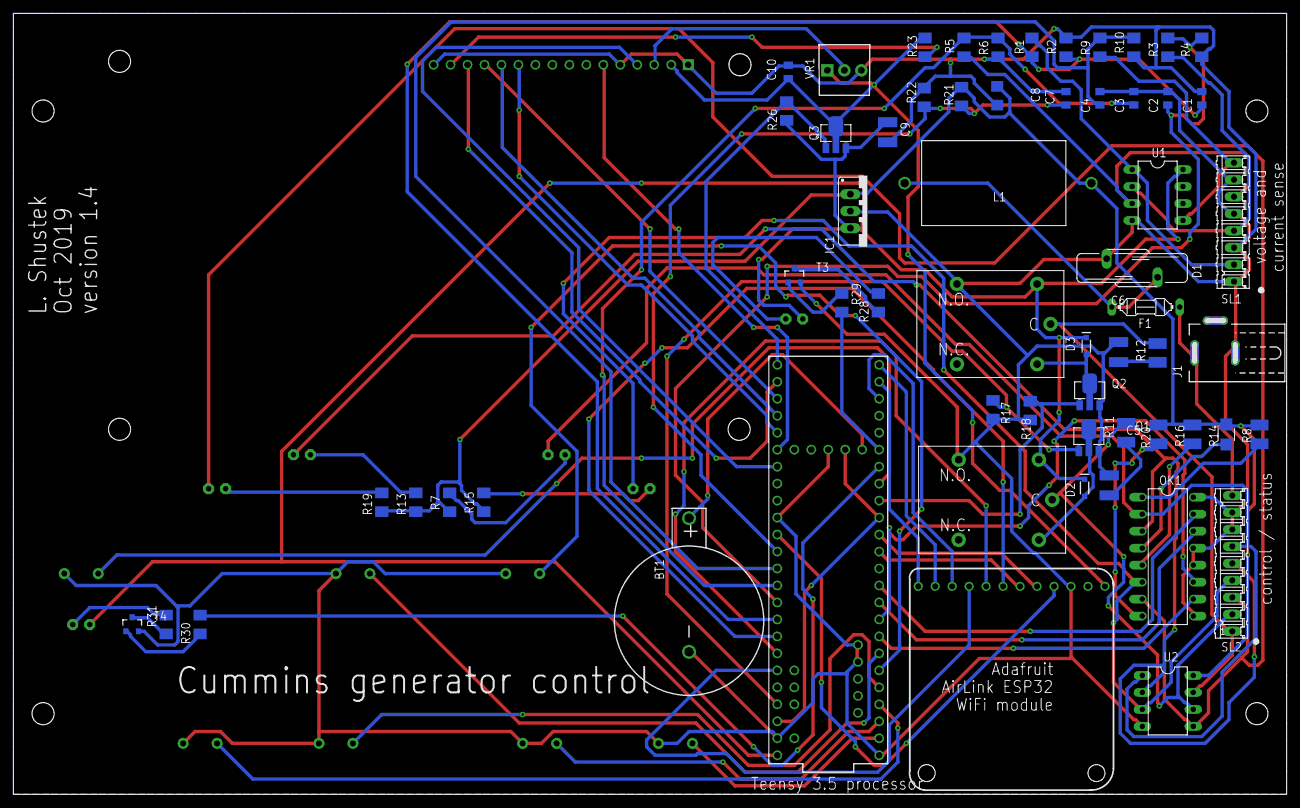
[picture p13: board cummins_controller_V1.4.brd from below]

Board: 2 copper layers, 190.5 x 116.8 mm, 75 parts (61 on the bottom side), 74 nets.

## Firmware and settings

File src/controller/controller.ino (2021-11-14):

/* -----------------------------------------------------------------------------------

       Controller for a standby generator

   This is the software for a custom-built controller that adds
   additional functionality to a standby generator system that uses
     - a Cummins "Quiet Connect" Series generator (20-40 KW), and
     - a Cummins RA series transfer switch

   The controller provides flexibility to program more sophisticated responses to power
   outages, such as  "wait one hour, then if the power is still out run the generator
   for a half hour every two hours until the utility power returns".

   It also acts as a web server, so the behavior can be monitored and controlled
   from anywhere using a standard web browser on a computer or smartphone.

   The controller box, which is connected only to signals inside the transfer switch,
   contains the following components:

   - a 4-line 20-character backlit LCD display
   - seven pushbuttons
   - six lights that indicate current status
   - voltage transducers for reading the utility and generator voltage levels
       using two TM2UA76 DIN-mounted units from Omni Instruments inside the transfer switch:
       https://www.omniinstruments.co.uk/tm2u-ac-voltage-isolated-transducer-rms.html
   - current transducers for the load, using two VC-100 toroids from Phidgets inside the transfer switch:
       https://www.phidgets.com/?tier=3&catid=16&pcid=14&prodid=378
   - two relays for controlling the generator and the transfer switch
   - an Adafruit AirLift ESP32 WiFi Co-Processor module
       https://www.adafruit.com/product/4201
   - a Teensy 3.5 32-bit RISC processor, running at 48 Mhz to reduce power consumption
        https://www.pjrc.com/store/teensy35.html
   - various noise-supression techniques were added, because switching 100+ amps nearby causes havoc with electronics
        Littelfuse SP721 transient voltage suppressor diode arrays on signals from outside the box
          https://www.mouser.com/datasheet/2/240/Littelfuse_TVS_Diode_Array_SP721_Datasheet.pdf-777167.pdf
        Vishay ILQ30 optical isolators on digital signals from outside the box
          https://www.mouser.com/datasheet/2/427/ild55-106155.pdf
        Littelfuse V18ZA3P MOV surge suppressor on the power input
          https://www.mouser.com/datasheet/2/240/Littelfuse_Varistor_ZA_Datasheet.pdf-467759.pdf
        Bourns 5900-152-RC 1.5 mH low-pass inductor (plus 33 uF capacitor) on the power input
          https://www.mouser.com/datasheet/2/54/900_series-777308.pdf
        Bud Industries CN-5711 metal enclosure surrounding our electronics
          https://www.budind.com/view/Die+Cast+Aluminum+Enclosure/CN-Series
        Ground plane pour on the unused area of both sides of the PC board
        A deadman watchdog timer that resets us if a glitch causes us to be catatonic
        Resetting the LCD display after power is switched
        Conductive transparent silver nanofilm on the window in front of the LCD display
          https://www.ebay.com/itm/272698061806
      All that seems to have done the job. It's not clear which really did the trick, but the rest can't hurt.

   The current draw from the generator battery is about 150 ma,
   increasing to 250 ma when the WiFi module is transmitting.

   The wiring inside the RA-style transfer box can include a toggle switch that
   disables this controller and uses the factory-provided functionality instead.
   See the interconnect schematic for details.

   For more information including photos and schematics, see
   https://github.com/LenShustek/generator_controller

   ----------------------------------------------------------------------------------------
*** CHANGE LOG ***

   1 Apr 2019, V1.0, L. Shustek
    - initial version
   12 Jul 2019, V2.0, L. Shustek
    - add Wifi support: we're a web server!
    - add support for deadman timer using the Analog Devices ADM6316 supervisor watchdog
    - cope with the generator taking a long time to shut off, and being on when we start up
   10 Oct 2019, V2.1, L. Shustek
    - allow MENU button to work when power is out
   28 Oct 2019, V2.2, L. Shustek
    - refresh power-out display status after MENU button
    - if GEN ON button during rest, set to cycle, not forever on
    - if GEN OFF button during run, set to cycle, not forever off
   16 Nov 2019, V2.3, L. Shustek
    - use the processor watchdog timer (instead of special hardware)
      to cause a reset if we're catatonic
    - implement the "at home" light and switch to simplify the user interface
    - show Wifi firmware level and MAC address
    - add a current limit that cancels generator rest periods if exceeded
    - Use IFTTT ("If This Then That") to send an SMS and email when certain events happen.
    - Accommodate transfer switches (like the RSS-series with controller) that keep control
      of the switch position.
    - Implement an exercise schedule, for switch/generator combinations that don't do it
      when we are wired into the system.
    - Add "extra info" to log file entries, whose interpretation depends on the type
    - Reset the Wifi module whenever we lose connection, and delay trying again.
    - Reset the LCD display whenever power is switched, because it is vulnerable
      to radiated electrical noise.
   23 Dec 2019, V2.4, L. Shustek
    - Don't create log entries for Wifi disconnect/connect; happens too frequently.
      Instead, keep statistics and report from the "show wifi info" submenu.
    - Add ; to end of &xx HTML character references like &nbsp; some browsers insist.
   08 Jan 2020, V2.5, L. Shustek
    - Don't test battery voltage until several seconds after power is off,
      otherwise something (the charger shutdown?) makes it incorrect.
    - Retry IFTTT trigger sends several times, a few seconds apart, and don't even
      do the first try until several seconds after we are connected to the network.
   10 Aug 2020, V2.6, L. Shustek
    - record and show the first and most recent date/time in the web visitor history
    1 Oct 2020, V2.7, L. Shustek
    - sort the visitor log by most recent date/time
   28 Aug 2021, V2.8, L. Shustek
    - After every few Wifi module reset attempts, drop and restore its power
      in an attempt to get it going again.
   
   Ideas:
   - better wifi rejoin attempts after power is restored (fails at the Lodge)
   - util_on and gen_on: also check voltage sense? Needed for RSS transfer switch?

   ------------------------------------------------------------------------------------------------
   Copyright (c) 2019,2020, Len Shustek
   The MIT License (MIT)
   Permission is hereby granted, free of charge, to any person obtaining a copy of this software
   and associated documentation files (the "Software"), to deal in the Software without
   restriction, including without limitation the rights to use, copy, modify, merge, publish,
   distribute, sublicense, and/or sell copies of the Software, and to permit persons to whom the
   Software is furnished to do so, subject to the following conditions:

   The above copyright notice and this permission notice shall be included in all copies or
   substantial portions of the Software.

   THE SOFTWARE IS PROVIDED "AS IS", WITHOUT WARRANTY OF ANY KIND, EXPRESS OR IMPLIED, INCLUDING
   BUT NOT LIMITED TO THE WARRANTIES OF MERCHANTABILITY, FITNESS FOR A PARTICULAR PURPOSE AND
   NONINFRINGEMENT. IN NO EVENT SHALL THE AUTHORS OR COPYRIGHT HOLDERS BE LIABLE FOR ANY CLAIM,
   DAMAGES OR OTHER LIABILITY, WHETHER IN AN ACTION OF CONTRACT, TORT OR OTHERWISE, ARISING
   FROM, OUT OF OR IN CONNECTION WITH THE SOFTWARE OR THE USE OR OTHER DEALINGS IN THE SOFTWARE.
   ------------------------------------------------------------------------------------------------*/

#include "generator.h"
#define VERSION "2.8"

// Here are the defaults that are put into non-volatile memory the first time.
// They may be changed using the configuration menu.
#define DEFAULT_GEN_DELAY_MINS 2*60  // delay until generator starts (if not "at home")
#define DEFAULT_GEN_RUN_MINS 30      // how long the generator runs for
#define DEFAULT_GEN_REST_MINS 3*60   // how long the generator rests for *uf not "at home")
#define DEFAULT_GEN_COOLDOWN_MINS 5  // how long the generator should cool down with no load
#define DEFAULT_UTIL_RETURN_MINS 12  // how long utility power must be on before using it
//                                      (should be more than TDEN=10 for RSS-type controllers)
#define DEFAULT_EXER_DURATION_MINS 0 // exercise duration: 0 (no exercise)
#define DEFAULT_EXER_WDAY 2          // exercise day: monday
#define DEFAULT_EXER_HOUR 11         // exercise hour: 11am
#define DEFAULT_EXER_WEEKS 2         // exercise periodicity: 2 weeks

// Here are fixed timeouts that can only be changed by recompiling.
#define TIMEOUT_GEN_START_SECS 30       // how long we give the generator to start
#define TIMEOUT_GEN_CONNECT_SECS 10     // how long we give the switch to connect to the generator
//                                         (should be more than TDNE=5 for RSS-type controllers)
#define TIMEOUT_UTIL_CONNECT_SECS 10    // how long we give the switch to connect to the utility
#define TIMEOUT_GEN_STOP_SECS 5         // how long we give the generator to stop
//                                         (not obeyed for RS22-type generators)

#define BATTERY_WARNING_LEVEL 11.9      // volts below which to warn about the starter battery
#define BATTERY_CHECK_DELAY_SECS 5      // delay after power fail before (and between) checking battery voltage
#define BATTERY_WARNING_HYSTERESIS 0.2  // hysteresis gap to avoid repeated warnings

#define GEN_REST_CURRENT_LIMIT 25       // amps above which we won't rest the generator

#define BUTTON_REPEAT_DELAY_MSEC 1000   // how long a button needs to be held before it repeats
#define BUTTON_REPEAT_PERIOD_MSEC 250   // the time between repeats

const byte button_pins[NUM_BUTTONS] = {
   GEN_BUTTON_PIN, MENU_BUTTON_PIN,
   LEFT_BUTTON_PIN, RIGHT_BUTTON_PIN,
   UP_BUTTON_PIN, DOWN_BUTTON_PIN,
   ATHOME_BUTTON_PIN };
enum button_indexes { // (used as byte values)
   GEN_BUTTON, MENU_BUTTON, LEFT_BUTTON, RIGHT_BUTTON, UP_BUTTON, DOWN_BUTTON, ATHOME_BUTTON };
bool button_awaiting_release[NUM_BUTTONS] = { // is button pushed and awaiting release?
   false };
unsigned long button_repeat_time[NUM_BUTTONS] = {0 }; // millis() when button should be repeated
bool button_webpushed[NUM_BUTTONS] = {false }; // buttons with pending "pushes" from the web

bool rungenrelay = false, connectgenrelay = false;
bool athome = false;
bool have_wifi_module = false;
bool exercising = false;
unsigned long exercise_start_millis;
bool ifttt_do_trigger = false;
const char *ifttt_data; // "failed", or "restored", or "test"
int ifttt_retry_count;
unsigned long ifttt_trytime_millis;
time_t last_poweron_time = 0; // When power last came on, either generator or utility

const char *event_names[] = { // must match enum in generator.h
   "controller started",
   "power failed",  "power restored",
   "generator start", "generator didn't start",
   "generator stop", "generator didn't stop",
   "generator cooldown",
   "connect to generator", "couldn't connect to generator", "gen connect with gen off!",
   "connect to utility", "couldn't connect to utility", "util connect with util off!",
   "WiFi module reset", "Wifi connected", "WiFi no connect", "WiFi disconnected",
   "assertion error", "watchdog reset", "starter battery read", "starter battery weak", "configuration updated",
   "exercise started", "exercise ended",
   "IFTTT queued:", "IFTTT sending:", "IFTTT sent", "IFTTT failed", "event:" };
// If the following gets a compile error, there is a mismatch with the enum declaration.
typedef char event_name_error[sizeof(event_names) / sizeof(event_names[0]) == EV_NUM_EVENTS ? 1 : -1];

//****  EEPROM storage for configuration info and the event log

#define EEPROM_SIZE 4096   // Teensy 3.5 uses the MK64FX512VMD12 Cortex M4
// processor running at 120 MHz, with 512K Flash, 192K RAM, and 4K EEPROM

#define CONFIG_HDR_LOC 0
struct { // local copy of the configuration data in EEPROM
   char id[6];  // "GENnn"      // unique header ID w/ format version number
#define ID_STRING "GEN04"       // change this to force the config and log to be rebuilt
   unsigned short gen_delay_mins;    // how many minutes to wait before turning generator on
   unsigned short gen_run_mins;      // how many minutes to run the generator for
   unsigned short gen_rest_mins;     // how many minutes to rest the generator between runs
   unsigned short gen_cooldown_mins; // how long the generator should cool down without load
   unsigned short util_return_mins;  // how many minutes before utility is reconnected
   byte exer_duration_mins;          // how many minutes to exercise for
   byte exer_wday;                   // which day of the week (sun=1)
   byte exer_hour;                   // starting at which hour (0=midnight to 23)
   byte exer_weeks;                  // every how many weeks (1..)
   time_t exer_last;                 // the last time we started an exercise period
#define FOREVER 0xffff
   unsigned short rsvd1, rsvd2, rsvd3; } config_hdr;

#define LOGFILE_HDR_LOC sizeof(config_hdr)
struct logfile_hdr_t logfile_hdr;
#define LOGFILE_LOC (LOGFILE_HDR_LOC+sizeof(logfile_hdr))
#define LOG_MAX ((EEPROM_SIZE - sizeof(config_hdr)) / sizeof(struct logentry_t))
struct logentry_t logfile[LOG_MAX];  // the log entries
int log_max_entries = LOG_MAX;

//------------------------------------------------------------------------------
//    watchdog timer routines, which cause a hard reset if we become catatonic
//------------------------------------------------------------------------------

void watchdog_setup(unsigned msec) { // enable the watchdog timer
   noInterrupts();
   WDOG_UNLOCK = 0xc520; // this two-part unlocking sequence must complete within 20 cycles
   WDOG_UNLOCK = 0xd928;
   __asm__ volatile ("nop\n\t"); // wait one bus cycle (1/2 CPU clock on Teensy)
   __asm__ volatile ("nop\n\t");
   __asm__ volatile ("nop\n\t");
   // we now have 256 bus cycles to program the watchdog timer
   WDOG_TOVALH = msec >> 16;    // how frequently the watchdog needs to be poked
   WDOG_TOVALL = msec & 0xffff; // given that we use the 1 Khz low-power oscillator (LPO)
   WDOG_WINH = 0;
   WDOG_WINL = 0;
   WDOG_PRESC = 0;
   WDOG_STCTRLH = WDOG_STCTRLH_WAITEN | WDOG_STCTRLH_STOPEN | WDOG_STCTRLH_DBGEN
                  | WDOG_STCTRLH_ALLOWUPDATE | WDOG_STCTRLH_WDOGEN;
   interrupts(); }

uint16_t watchdog_counter(void) { // how many times the watchdog has done a reset since poweron
   return WDOG_RSTCNT; }

void watchdog_poke(void) { // poke the watchdog to prevent a reset
   // The K64 processor has a bug: if you refresh the watchdog timer too frequently (more than once
   // per 1 msec watchdog clock timer period?) then the refresh is ignored and the watchdog timer
   // will eventually fire. The bug is discussed in these forums:
   // https://community.nxp.com/thread/474814
   // https://www.silabs.com/community/mcu/8-bit/knowledge-base.entry.html/2016/11/28/wdt_e101_-_restricti-Vqe5
   // My solution is to skip the refresh if the watchdog counter hasn't advanced by at least two.
   static uint16_t last_timerlow = 0;
   noInterrupts();
   uint16_t current_timerlow = WDOG_TMROUTL;
   if ((uint16_t)(current_timerlow - last_timerlow) > 2
         && digitalReadFast(DOWN_BUTTON_PIN) != 0  // TEMP to test watchdog timer
      ) { // don't refresh too frequently
      last_timerlow = current_timerlow;
      WDOG_REFRESH = 0xa602; // this two-part refresh sequence must complete within 20 cycles
      WDOG_REFRESH = 0xb480; }
   interrupts(); }

//-----------------------------------------------------------------------
//    LCD display routines
//-----------------------------------------------------------------------

// We keep a software simulation of the LCD for web access,
// and write to the real LCD hardware only if we have it.

char lcdbuf[4][21]; // our simulated LCD buffer, with 0 string terminators
int lcdrow /* 0..3 */, lcdcol /* 0..19 */;

#if LCD_HW
LiquidCrystal lcdhw (LCD_RS, LCD_EN, LCD_D4, LCD_D5, LCD_D6, LCD_D7);
bool lcdWiFi_on = false;

void lcd_start(void) {
   static uint8_t downarrow_char[8] = {
      B00000,
      B00100,
      B00100,
      B00100,
      B10101,
      B01110,
      B00100,
      B00000 };
   static uint8_t uparrow_char[8] = {
      B00100,
      B01110,
      B10101,
      B00100,
      B00100,
      B00100,
      B00100,
      B00000 };

   lcdhw.begin(20, 4); // start LCD display
   lcdhw.createChar(DOWNARROW[0], downarrow_char);
   lcdhw.createChar(UPARROW[0], uparrow_char);
   lcdhw.noCursor(); }

void lcd_restart(void) {
   lcd_start(); // restart the hardware
   for (int row = 0; row < 4; ++row) // copy from our internal buffer to the display
      for (int col = 0; col < 20; ++col) {
         lcdhw.setCursor(col, row);
         lcdhw.print(lcdbuf[row][col]); }
   lcdhw.setCursor(lcdcol, lcdrow); }
#endif

void lcdsetrow( byte row) {
   assert(row <= 3, "bad lcdsetrow", row);
   #if LCD_HW
   lcdhw.setCursor(0, row);
   #endif
   lcdrow = row; lcdcol = 0; }

void lcdsetCursor(byte col, byte row) {
   assert (row <= 3 && col <= 19, "bad lcdsetcursor", (col << 16) | row);
   #if LCD_HW
   lcdhw.setCursor(col, row);
   #endif
   lcdcol = col; lcdrow = row; }

void lcdclear(void) {
   #if LCD_HW
   lcdhw.clear();
   #endif
   memset(lcdbuf, ' ', sizeof(lcdbuf)); // blank the buffer
   for (int row = 0; row < 4; ++row) lcdbuf[row][20] = 0; // insert string terminators
   lcdrow = lcdcol = 0; }

void lcdblink(void) {
   #if LCD_HW
   lcdhw.blink();
   #endif
}
void lcdnoBlink(void) {
   #if LCD_HW
   lcdhw.noBlink();
   #endif
}

bool showing_screen = false; // was the screen the last thing shown?

void lcddumpscreen(void) { // dump the screen image to the terminal
#define CURSOR_UP7 "\e[7A" // works for puTTY VT100, but not for Arduino's Serial Monitor
   #if DEBUG && !LCD_HW
   if (showing_screen) Serial.println(CURSOR_UP7); // rewrite the screen
   Serial.println("|--------------------|");
   for (int row = 0; row < 4; ++row) {
      Serial.print('|');
      for (char *src = lcdbuf[row]; *src; ++src)
         Serial.print( // translate arrows to best ASCII substitutes
            *src == LEFTARROW[0] ? '<' :
            *src == RIGHTARROW[0] ? '>' :
            *src == UPARROW[0] ? '^' :
            *src == DOWNARROW[0] ? 'v' :
            *src
         );
      Serial.println('|'); }
   Serial.println("|--------------------|");
   showing_screen = true;
   #endif
}

void lcdprint(char ch) {
   assert(lcdcol < 20 && lcdrow < 4, "bad lcdprint ch", (lcdcol << 16) | lcdrow);
   #if LCD_HW
   lcdhw.print(ch);
   #endif
   /* if (lcdcol < 20)*/ lcdbuf[lcdrow][lcdcol] = ch;
   if (lcdcol < 19) ++lcdcol;
   lcddumpscreen(); }

void lcdprint(const char *msg) {
   int length = strlen(msg);
   if (length > 20 - lcdcol) {
      Serial.print(length); Serial.print("=len, lcdcol="); Serial.println(lcdcol);
      Serial.println(msg); }
   assert (length <= 20 - lcdcol, "bad lcdprint", (length << 16) | lcdcol);
   #if LCD_HW
   lcdhw.print(msg);
   #endif
   //int length = min((int)strlen(msg), 20 - lcdcol);
   for (int ndx = 0; length--; ++ndx ) {
      if (lcdcol < 20) lcdbuf[lcdrow][lcdcol] = msg[ndx];
      if (lcdcol < 19) ++lcdcol; }
   lcddumpscreen(); }

void lcdprint(byte row, const char *msg) {
   lcdsetrow(row);
   lcdprint(msg); }

void lcdprintf(byte row, const char *msg, ...) {
   char buf[40];
   va_list arg_ptr;
   va_start(arg_ptr, msg);
   vsnprintf(buf, sizeof(buf), msg, arg_ptr);
   assert(strlen(buf) <= 20, "bad lcdprint(msg,..)");
   lcdprint(row, buf);
   va_end(arg_ptr); }

void lcdWiFi_poweron(void) { // power on display and WiFi module
   pinMode(POWER_DISPLAY_WIFI, OUTPUT);
   digitalWrite(POWER_DISPLAY_WIFI, 0); }
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
void loop(void) {

   // show the various headline messages

#define HEADLINE_UPDATE_MSEC 400  // update them this often
#define HEADLINE_CHANGE_TIMES 5  // and change every this many times
   // the message types
   enum headline_types {PLACENAME, DATETIME, BATTERYWARN, EXERCISE, WRAPAROUND };
   // pointers to the booleans that say whether to show a message type
   static bool alwaystrue = true;
   static bool *headline_doit[] = {&alwaystrue, &alwaystrue, &do_battery_warning, &exercising };
   static int headline = PLACENAME, headline_changecount = 0;
   static unsigned long headline_time = 0;

   if (millis() - headline_time > HEADLINE_UPDATE_MSEC) {  // time to update
      if (++headline_changecount >= HEADLINE_CHANGE_TIMES) { // time to change
         lcddumpscreen();
         headline_changecount = 0;
         if (headline == BATTERYWARN || headline == EXERCISE) lcdclear();
         do { // find the next one we should do
            if (++headline >= WRAPAROUND) headline = PLACENAME; }
         while (!*headline_doit[headline]);
         check_exercise_startstop(false); }
      headline_time = millis();
      switch (headline) { // update the display
         case PLACENAME: center_message(0, TITLE); show_voltage_current(2);
            break;
         case DATETIME: show_datetime(0, now(), false); show_voltage_current(2);
            break;
         case BATTERYWARN: show_battery_warning(1);
            break;
         case EXERCISE: center_message(1, "Exercising generator");
            timeleft_message("time left",
                             MINS_TO_SECS(config_hdr.exer_duration_mins) - (millis() - exercise_start_millis) / 1000);
            break; } }

   idle();

   if (!util_on.val) {  // if power is out,
      util_failed();    // then spring into action
      lcdclear(); }

   byte button = check_for_button();
   if (button == MENU_BUTTON) menu_pushed();
   if (button == GEN_BUTTON) gen_pushed();

   delay(SMIDGE); }

//*

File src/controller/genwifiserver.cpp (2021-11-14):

// file:genwifi.c
/* ----------------------------------------------------------------------------------------
   web routines

   This runs almost like a separate process by calling process_web() periodically.
   (Unfortunately some WiFiNINA calls block for many seconds!)

   As a web server we provide the current status page as the home page. There are also these subpages:
     /log         show the event log
     /visitors    show the list of IP addresses who visited
     /pushbutton  push the button in the POST request "button=x"
                  and return the status page after a delay
                  that allows the button action to happen

   Only one client is supported at a time, and the WiFiNINA library has several bugs:
     - long transfers (ie images) have to be broken up and separated in time
     - it won't accept two simultaneous connections from the client, which the Chrome
       brower does for images

   Also, the wifi module can get itself into a state where even a reset won't get it working.
   It that case we drop and restore its power to try to get it running again.

   We also can act as a web client (browser) to issue triggers to IFTTT that cause emails
   and/or text messages to be sent.

   See the main module for other details and the change log.
   ----------------------------------------------------------------------------------------
   Copyright (c) 2019,2020 Len Shustek
   The MIT License (MIT)
   Permission is hereby granted, free of charge, to any person obtaining a copy of this software
   and associated documentation files (the "Software"), to deal in the Software without
   restriction, including without limitation the rights to use, copy, modify, merge, publish,
   distribute, sublicense, and/or sell copies of the Software, and to permit persons to whom the
   Software is furnished to do so, subject to the following conditions:

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
   THE SOFTWARE IS PROVIDED "AS IS", WITHOUT WARRANTY OF ANY KIND, EXPRESS OR IMPLIED, INCLUDING
   BUT NOT LIMITED TO THE WARRANTIES OF MERCHANTABILITY, FITNESS FOR A PARTICULAR PURPOSE AND
   NONINFRINGEMENT. IN NO EVENT SHALL THE AUTHORS OR COPYRIGHT HOLDERS BE LIABLE FOR ANY CLAIM,
   DAMAGES OR OTHER LIABILITY, WHETHER IN AN ACTION OF CONTRACT, TORT OR OTHERWISE, ARISING
   FROM, OUT OF OR IN CONNECTION WITH THE SOFTWARE OR THE USE OR OTHER DEALINGS IN THE SOFTWARE.
   ------------------------------------------------------------------------------------------------*/

/* WiFi.status() return codes
        WL_NO_SHIELD = 255,
        WL_NO_MODULE = WL_NO_SHIELD, // 255
        WL_IDLE_STATUS = 0, // 0
        WL_NO_SSID_AVAIL, // 1
        WL_SCAN_COMPLETED, // 2
        WL_CONNECTED, // 3
        WL_CONNECT_FAILED, // 4
        WL_CONNECTION_LOST, // 5
        WL_DISCONNECTED, // 6
        WL_AP_LISTENING, // 7
        WL_AP_CONNECTED,  // 8
        WL_AP_FAILED //  9
*/

#include "generator.h"

#if WIFI

#define MAX_IP_ADDRESSES 50     // maximum visitors we keep track of
#define DELAYED_RSP_MSEC 1000   // how long to delay an HTTP response for a button push to be processed

WiFiServer server(WIFI_PORT); // 80 is standard; others are more secure
WiFiClient client; // static client allows only one at a time when we're a server

IPAddress remote_IP;
enum {WEB_NOT_CONNECTED, WEB_AWAITING_CONNECTION,   // WiFi network connection states
      WEB_AWAITING_CLIENT, WEB_PROCESSING_REQUEST   // web server states
     } web_status = WEB_NOT_CONNECTED;

enum  request_type_t {REQ_UNKNOWN, REQ_ROOT, REQ_VISITORS, REQ_LOG, REQ_PUSHBUTTON, REQ_SETPASS, REQ_FAVICON, REQ_BUTTONIMAGE };
const char *request_type_names[] = {"unknown", "root", "visitors", "log", "pushbutton", "setpass", "favicon", "buttonimage", "???" };

enum response_type_t {RSP_UNKNOWN, RSP_STATUS, RSP_VISITORS, RSP_LOG, RSP_FAVICON, RSP_BUTTONIMAGE, RSP_ASKPASS, RSP_NONE };
const char *response_type_names[] = {"unknown", "status", "visitors", "log", "favicon", "buttonimage", "askpass", "no_response", "???" };

bool delayed_response = false;
unsigned long delayed_sendtime;

time_t next_connect_time = 0;  // when to next try to connect to the WiFi network

struct client_t { // history of the clients whose web browsers made requests
   IPAddress ip_address;
   long count;
   time_t first_time, recent_time;
   bool gave_password; }
clients[MAX_IP_ADDRESSES],
        *current_client;
long requests_processed = 0;
long wifi_connects = 0, wifi_connectfails = 0, wifi_disconnects = 0, wifi_resets = 0;
long ifttt_queues = 0, ifttt_sends = 0, ifttt_successes = 0, ifttt_failures = 0;

char linebuf[MAXLINE];

bool client_write(WiFiClient *pclient, const char *buf, int length, bool show) {
#define CHUNKSIZE 500 // to get around WiFiNINA bugs...
   while (length > 0) {
      //Serial.print(length); Serial.print(" bytes to write; ");
      if (!pclient->connected()) {
         //Serial.print("at time "); Serial.print((float)millis() / 1000);
         //Serial.println(" client no longer connected");
         return false; }
      int bytes_done = pclient->write(buf, length > CHUNKSIZE ? CHUNKSIZE : length); //TEMP server.write???
      if (HTML_SHOW_RSP) {
         showing_screen = false;
         Serial.print("at time "); Serial.print((float)millis() / 1000); Serial.print(" wrote ");
         if (show) {
            Serial.print(bytes_done); Serial.print(" bytes: ");
            if (bytes_done < MAXLINE) Serial.write(buf, bytes_done);
            else {
               Serial.write(buf, MAXLINE);
               Serial.write("...\n"); } }
         else {
            Serial.print(bytes_done); Serial.print(" bytes of binary data\n"); } }
      length -= bytes_done;
      buf += bytes_done;
      delay(10); // time for something to happen on the co-processor??
   }
   return true; }

void client_printf(WiFiClient *pclient, const char *format, ...) {
   char buf[MAXLINE];
   va_list argptr;
   va_start(argptr, format);
   vsnprintf(buf, MAXLINE, format, argptr);
   client_write(pclient, buf, strlen(buf), true);
   va_end(argptr); }

char *expand_arrows_and_blanks(char *msg) { // expand our arrow symbols into HTML arrows, blanks into &nbsp
   // WARNING: returns pointer to a static string!
   static char outmsg[MAXLINE];
   char *dst = outmsg;
   for (char *src = msg; *src; ++src) {
      if (*src == LEFTARROW[0]) {
         strcpy(dst, "&#8592;"); dst += 6; }
      else if (*src == UPARROW[0]) {
         strcpy(dst, "&#8593;"); dst += 6; }
      else if (*src == RIGHTARROW[0]) {
         strcpy(dst, "&#8594;"); dst += 6; }
      else if (*src == DOWNARROW[0]) {
         strcpy(dst, "&#8595;"); dst += 6; }
      else if (*src == ' ') {
         strcpy(dst, "&nbsp;"); dst += 5; }
      else *dst++ = *src; }
   *dst = 0;
   return outmsg; }
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

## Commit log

2020-01-01 Cummins generator controller
    [cummins_controller_V1.4.brd, cummins_controller_V1.4.sch, interconnect_RA_V1.2.sch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]
2021-11-14 retry IFTTT, sort visitor history by date, power cycle WiFi when it won't start
    [controller.ino, generator.h, genwifiserver.cpp]

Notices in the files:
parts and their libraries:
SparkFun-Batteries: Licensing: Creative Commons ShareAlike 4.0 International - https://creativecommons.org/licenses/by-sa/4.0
